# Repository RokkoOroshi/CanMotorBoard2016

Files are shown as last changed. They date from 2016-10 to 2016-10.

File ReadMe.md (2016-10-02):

# CAN Motor Driver Board

can通信機能対応2chモータドライバ基板

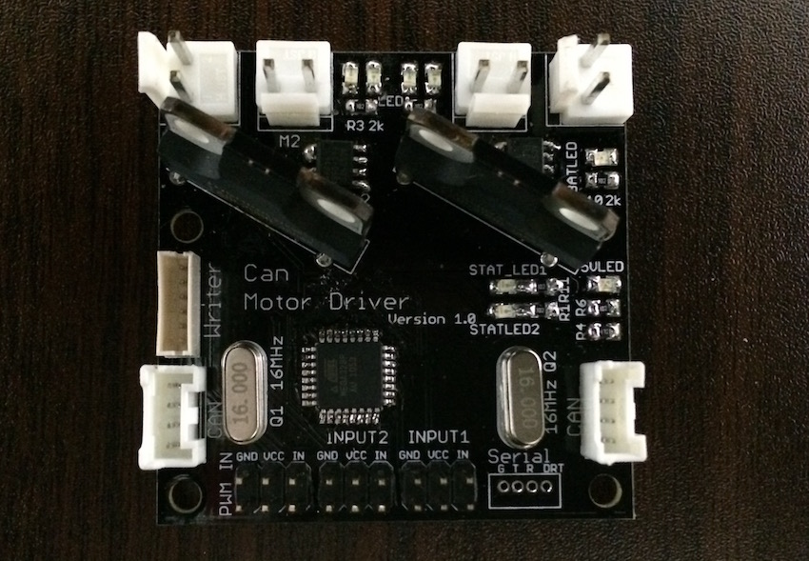
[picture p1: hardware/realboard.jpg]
基板


## IO

- DCモータ2ch制御 avg3.0A,peek4.5A (TA8429H使用)(放熱してないので無理です..)
- モータ電源ポート2個
- CAN通信ポート2個
- avr ISP 書き込みポート
- Arduino書き込み対応シリアル通信ポート
- 汎用入出力4ch(内2chはプルダウン済み)
- アナログ入力2ch
- 状態表示用LED 2ch

## 製作動機

- 製作負担軽減（と個人的な趣好）のために既存のユニバーサル基板からプリント基板への移行したい
- 配線の簡略化、基板との双方向通信実現のためにCAN通信を導入したい

## 製作時の配慮
- ストックが多数あるTA8429Hを使う
- PWM入力に対応し、今までと同じ方法でも使用できるようにする
- Arduino開発環境に対応し、初心者でも扱いやすいように

## License

- MIT

## 使用ライブラリ等

- CAN_BUS_Shield : MIT : https://github.com/Seeed-Studio/CAN_BUS_Shield
- MsTimer2 : LGPL : http://playground.arduino.cc/Main/MsTimer2
- pins_arduino.h : LGPL
- Arduino-SerialCommand : ? : https://github.com/kroimon/Arduino-SerialCommand

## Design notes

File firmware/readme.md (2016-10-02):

# CAN Motor Board Firmware

## Arduino IDE での使用方法
1. Arduino IDEをダウンロード・インストール
2. install.batを管理者として実行（Arduino IDEのフォルダ下に必要なファイルのシンボリックリンクを作ってる）
3. Arduino IDEのボード選択メニューで"RokkoOroshiCanMotorBoard"を選択

これで各ピンのシンボルが自動で定義され、各種ライブラリをincludeできるようになる。

また、この基板はArduinoProMini互換であるが、ブートローダーは書き込み速度を通常より高速にしたものを使用しているため、IDEでArduinoProMiniを選択した場合書き込みできないので注意。

## ライブラリ
Arduino IDEのメニュー include library から選択できるようになっているはず。

現状、依存ライブラリをhoge.ino内でincludeしないとコンパイルエラーになる

### Motor
* 基板に搭載された２つのモーター出力を制御する関数を定義している
* モーターの出力状態を管理するために、この関数を通じてモーターを制御すること。

### CanCommunication

* CAN上で各ノードが相互に通信するためのライブラリ
* 通信規格は独自の簡易的なものを使用、詳細はcan_communication_def.h参照
* SPI.h(標準ライブラリ), mcp_can.h(CAN_BUS_SHEILDライブラリ) に依存

## その他
* このフォルダ下にhardware_profile.h, can_communication_dfe.hがあるが、これは内容確認用に置いているだけ。RokkoOroshiCanMotorBoard下の深いところに同じファイルがあり、ArduinoIDEではそちらを参照している。このフォルダ下のものは最新でない可能性があるので注意。
* ピン配置はhardware_profile.hを見ると早い
* can_communication_defには通信規格を書いている

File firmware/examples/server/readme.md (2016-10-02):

# 4WD ロボット制御サンプル

* 基板二つを接続して4WDの足回りを動かせるようにする
* 前二つ、後ろ二つをそれぞれ同じ基板に接続
* 右モーターM1, 左モーターM2

#server

* pcで動く
* nodejs 使用

~~~
cd server
npm install
node main.js
# 表示されるリストからシリアル通信の接続先を選択
# ブラウザでlocalhost:8080 にアクセス
~~~

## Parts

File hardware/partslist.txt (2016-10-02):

抵抗

R1	1k	状態LED
R2	10k	MCP2515RESETプルアップ
R3	1k	モータ動作方向LED
R4	4.7k	CAN通信slope
R5	1k	モータ動作方向LED
R6	1k	ロジック電源LED
R7	1k	PWM入力プルダウン
R8	10k	マイコンRESETプルアップ
R9	1k	PWM入力プルダウン
R10	1k	モータ電源LED
R11	1k	状態LED
R14	2k	モータ電源電圧検出用分圧
R15	1k	モータ電源電圧検出用分圧

1k	9個
2k	1個
4.7k	1個
10k	2個

コンデンサ

C1	0.1uF	Arduino書き込み用DRT
C2	0.1uF	パスコン
C3	22pF	水晶発信器負荷
C4	22pF	 ..
C5	22pF	 ..
C6	22pF	 ..

0.1uF	2個
22pF	4個

その他
ATMega328p	1個	メインマイコン
TA8429H		2個	モータドライバ
MCP2551		1個	CAN通信
MCP2515		1個	CAN通信
ACS712		2個	電流センサ（オプション的扱い）
水晶発信器16MHz	2個
チップLED	8個	モータ方向x4, 電源x2, 汎用x2
ダイオード	1個	PWM入力ポートの電源逆流対策
B2P-VH		4個	モータ、モータ電源
B4B-ZR		1個	Arduino書き込み、シリアル通信
B6B-ZR		1個	ISP書き込み
B4B-PASK	2個	CAN通信
ピンヘッダ2x3	3個	PWMIN,ADC,DIO

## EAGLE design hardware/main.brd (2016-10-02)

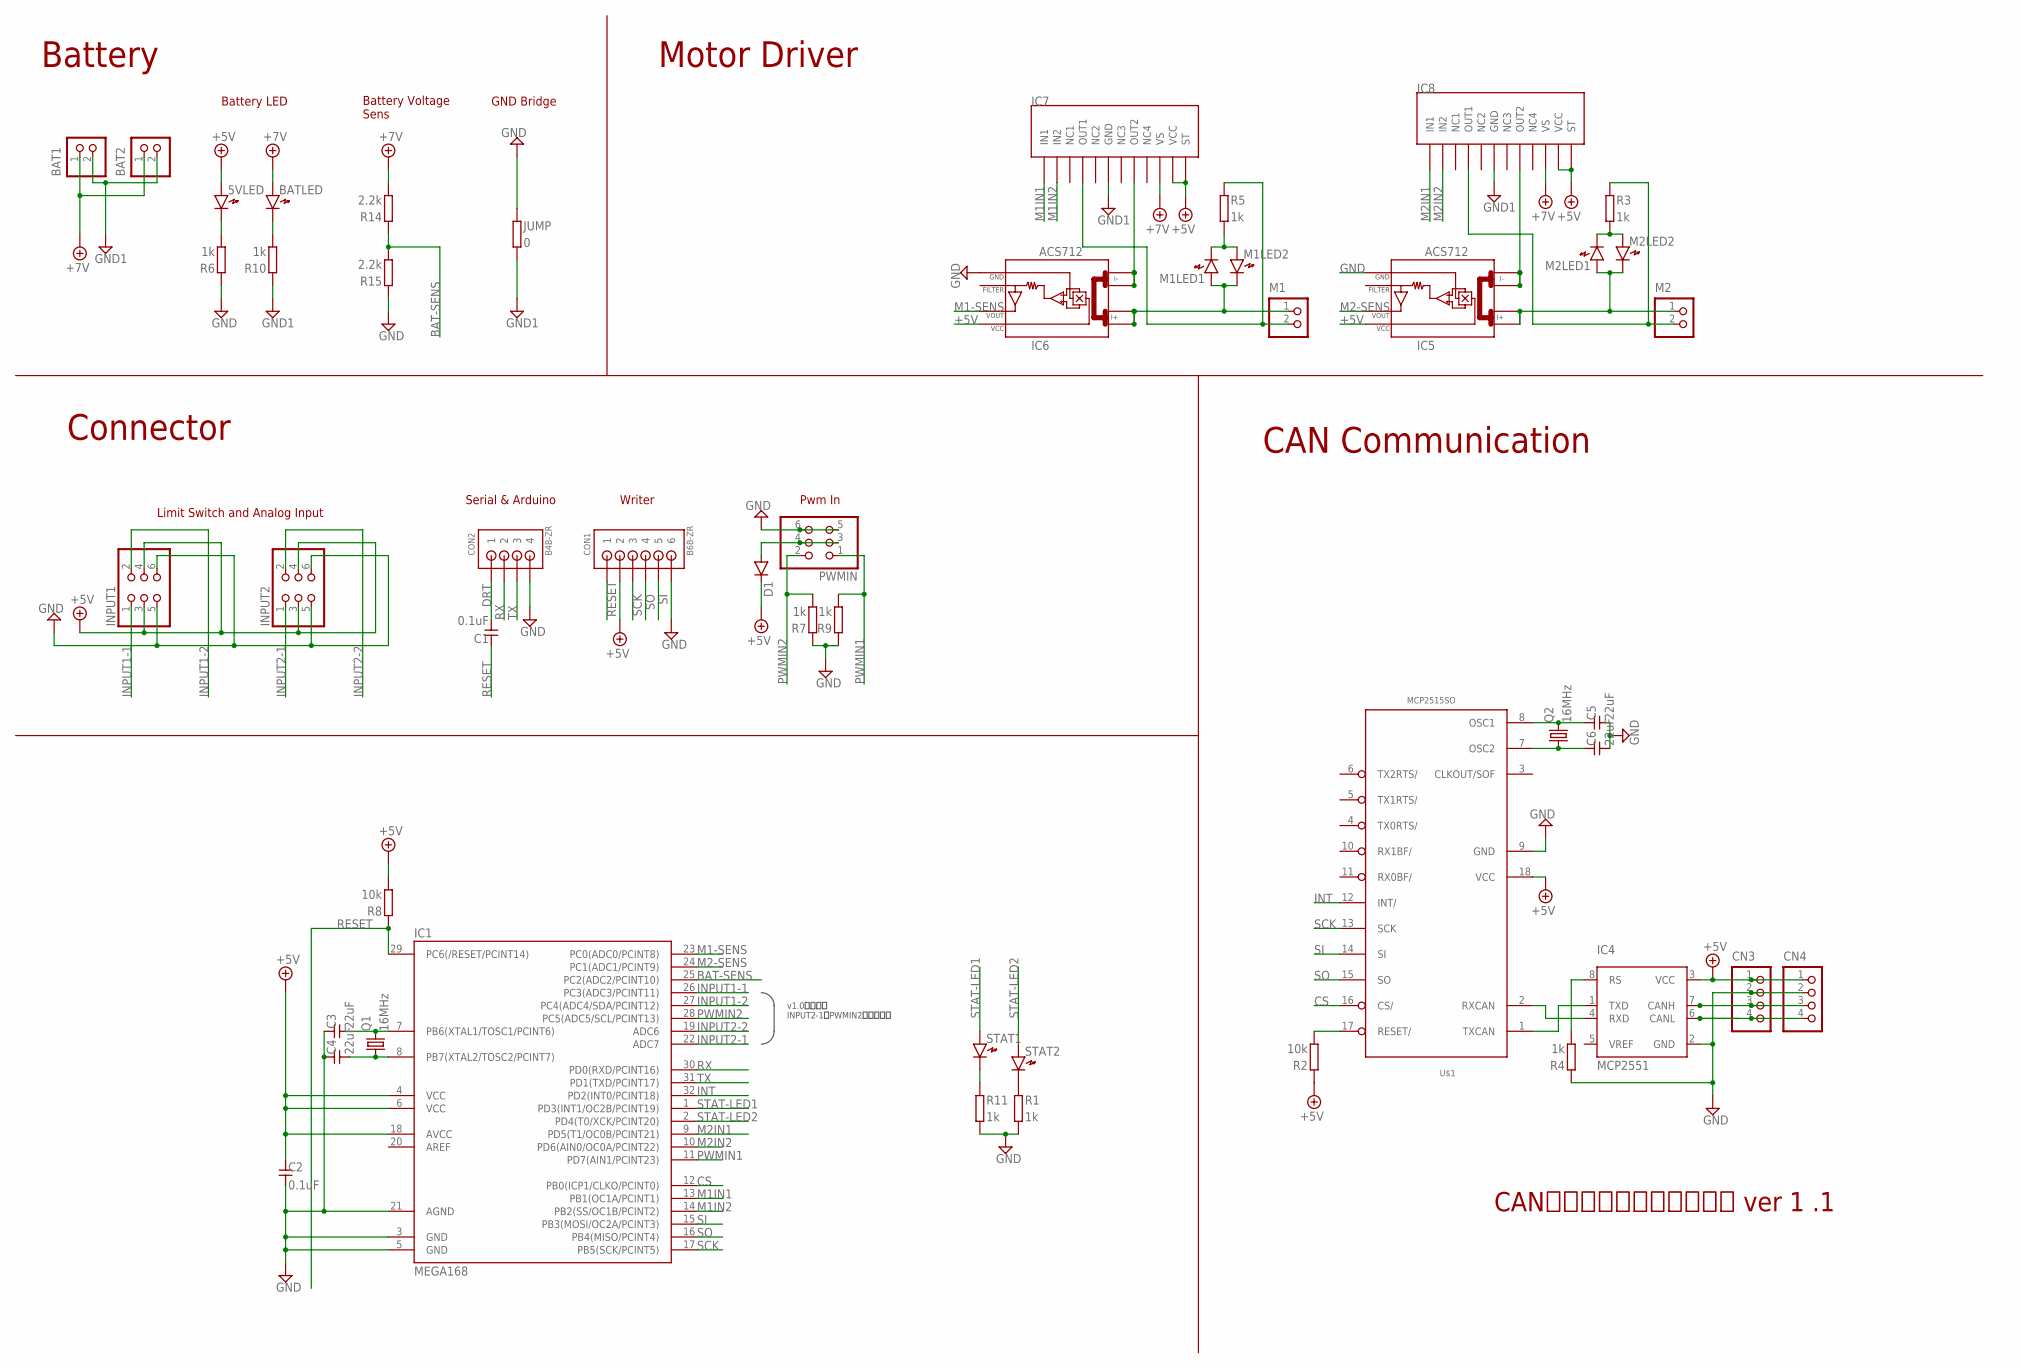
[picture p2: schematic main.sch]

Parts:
5VLED: LED2012
BAT1, BAT2: B2P-VH
BATLED: LED2012
C1, C2: 0.1uF; SMD2012
C3, C4, C5, C6: 22uF; SMD2012
CN3, CN4: B4B-PH-K-S
CON1: B6B-ZR
CON2: B4B-ZR
D1: DIODESOD123; SOD-123
IC1: MEGA168; TQFP32-08
IC4: MCP2551; SOIC
IC5, IC6: ACS712; SO08
IC7, IC8: TA8429H
INPUT1, INPUT2: PINHD-2X3; 2X03
JUMP: 0; SMD2012
M1, M2: B2P-VH
M1LED1, M1LED2, M2LED1, M2LED2: LED2012
PWMIN: PINHD-2X3; 2X03
Q1, Q2: 16MHz; HC49/S
R1, R3, R4, R5, R6, R7, R9, R10, R11: 1k; SMD2012
R2, R8: 10k; SMD2012
R14, R15: 2.2k; SMD2012
STAT1, STAT2: LED2012
U$1: MCP2515SO; SO18L

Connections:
+5V: 5VLED.A, C2.1, CN3.1, CN4.1, CON1.2, D1.C, IC1.4 (VCC), IC1.6 (VCC), IC1.18 (AVCC), IC4.3 (VCC), IC5.8 (VCC), IC6.8 (VCC), IC7.P$11 (VCC), IC7.P$12 (ST), IC8.P$11 (VCC), IC8.P$12 (ST), INPUT1.3, INPUT1.4, INPUT2.3, INPUT2.4, R2.1, R8.2, U$1.18 (VCC)
+7V: BAT1.1, BAT2.1, BATLED.A, IC7.P$10 (VS), IC8.P$10 (VS), R14.2
BAT-SENS: IC1.25 (PC2(ADC2/PCINT10)), R14.1, R15.2
CS: IC1.12 (PB0(ICP1/CLKO/PCINT0)), U$1.16 (CS/)
DRT: C1.2, CON2.1
GND: C2.2, C3.1, C4.1, C5.2, C6.2, CN3.2, CN4.2, CON1.6, CON2.4, IC1.3 (GND), IC1.5 (GND), IC1.21 (AGND), IC4.2 (GND), IC5.5 (GND), IC6.5 (GND), INPUT1.5, INPUT1.6, INPUT2.5, INPUT2.6, JUMP.1, PWMIN.5, PWMIN.6, R1.2, R4.1, R6.1, R7.1, R9.1, R11.2, R15.1, U$1.9 (GND)
INPUT1-1: IC1.26 (PC3(ADC3/PCINT11)), INPUT1.1
INPUT1-2: IC1.27 (PC4(ADC4/SDA/PCINT12)), INPUT1.2
INPUT2-1: IC1.22 (ADC7), INPUT2.1
INPUT2-2: IC1.19 (ADC6), INPUT2.2
INT: IC1.32 (PD2(INT0/PCINT18)), U$1.12 (INT/)
M1-SENS: IC1.23 (PC0(ADC0/PCINT8)), IC6.7 (VOUT)
M1IN1: IC1.13 (PB1(OC1A/PCINT1)), IC7.P$1 (IN1)
M1IN2: IC1.14 (PB2(SS/OC1B/PCINT2)), IC7.P$2 (IN2)
M2-SENS: IC1.24 (PC1(ADC1/PCINT9)), IC5.7 (VOUT)
M2IN1: IC1.9 (PD5(T1/OC0B/PCINT21)), IC8.P$1 (IN1)
M2IN2: IC1.10 (PD6(AIN0/OC0A/PCINT22)), IC8.P$2 (IN2)
MGND: BAT1.2, BAT2.2, IC7.P$6 (GND), IC8.P$6 (GND), JUMP.2, R10.1
unnamed: C3.2, IC1.7 (PB6(XTAL1/TOSC1/PCINT6)), Q1.2
unnamed: C4.2, IC1.8 (PB7(XTAL2/TOSC2/PCINT7)), Q1.1
unnamed: IC8.P$4 (OUT1), M2.2, R3.1
unnamed: IC6.1 (I+_0), IC6.2 (I+_1), M1.1, M1LED1.A, M1LED2.K
unnamed: D1.A, PWMIN.3, PWMIN.4
unnamed: IC5.1 (I+_0), IC5.2 (I+_1), M2.1, M2LED1.A, M2LED2.K
unnamed: IC4.1 (TXD), U$1.1 (TXCAN)
unnamed: IC4.4 (RXD), U$1.2 (RXCAN)
unnamed: 5VLED.K, R6.2
unnamed: R1.1, STAT2.K
unnamed: CN3.4, CN4.4, IC4.6 (CANL)
unnamed: CN3.3, CN4.3, IC4.7 (CANH)
unnamed: M1LED1.K, M1LED2.A, R5.2
unnamed: IC7.P$4 (OUT1), M1.2, R5.1
unnamed: R2.2, U$1.17 (RESET/)
unnamed: M2LED1.K, M2LED2.A, R3.2
unnamed: C6.1, Q2.1, U$1.7 (OSC2)
unnamed: BATLED.K, R10.2
unnamed: IC6.3 (I-_0), IC6.4 (I-_1), IC7.P$8 (OUT2)
unnamed: IC5.3 (I-_0), IC5.4 (I-_1), IC8.P$8 (OUT2)
unnamed: C5.1, Q2.2, U$1.8 (OSC1)
unnamed: IC4.8 (RS), R4.2
unnamed: R11.1, STAT1.K
PWMIN1: IC1.11 (PD7(AIN1/PCINT23)), PWMIN.1, R9.2
PWMIN2: IC1.28 (PC5(ADC5/SCL/PCINT13)), PWMIN.2, R7.2
RESET: C1.1, CON1.1, IC1.29 (PC6(/RESET/PCINT14)), R8.1
RX: CON2.2, IC1.30 (PD0(RXD/PCINT16))
SCK: CON1.3, IC1.17 (PB5(SCK/PCINT5)), U$1.13 (SCK)
SI: CON1.5, IC1.15 (PB3(MOSI/OC2A/PCINT3)), U$1.14 (SI)
SO: CON1.4, IC1.16 (PB4(MISO/PCINT4)), U$1.15 (SO)
STAT-LED1: IC1.1 (PD3(INT1/OC2B/PCINT19)), STAT1.A
STAT-LED2: IC1.2 (PD4(T0/XCK/PCINT20)), STAT2.A
TX: CON2.3, IC1.31 (PD1(TXD/PCINT17))

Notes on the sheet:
Limit Switch and Analog Input
Writer
CAN通信対応モータドライバ ver 1 .1
Battery
Motor Driver
CAN Communication
Connector
GND Bridge
Battery Voltage Sens
Battery LED
Serial & Arduino
Pwm In
v1.0から変更 INPUT2-1とPWMIN2を入れ替え

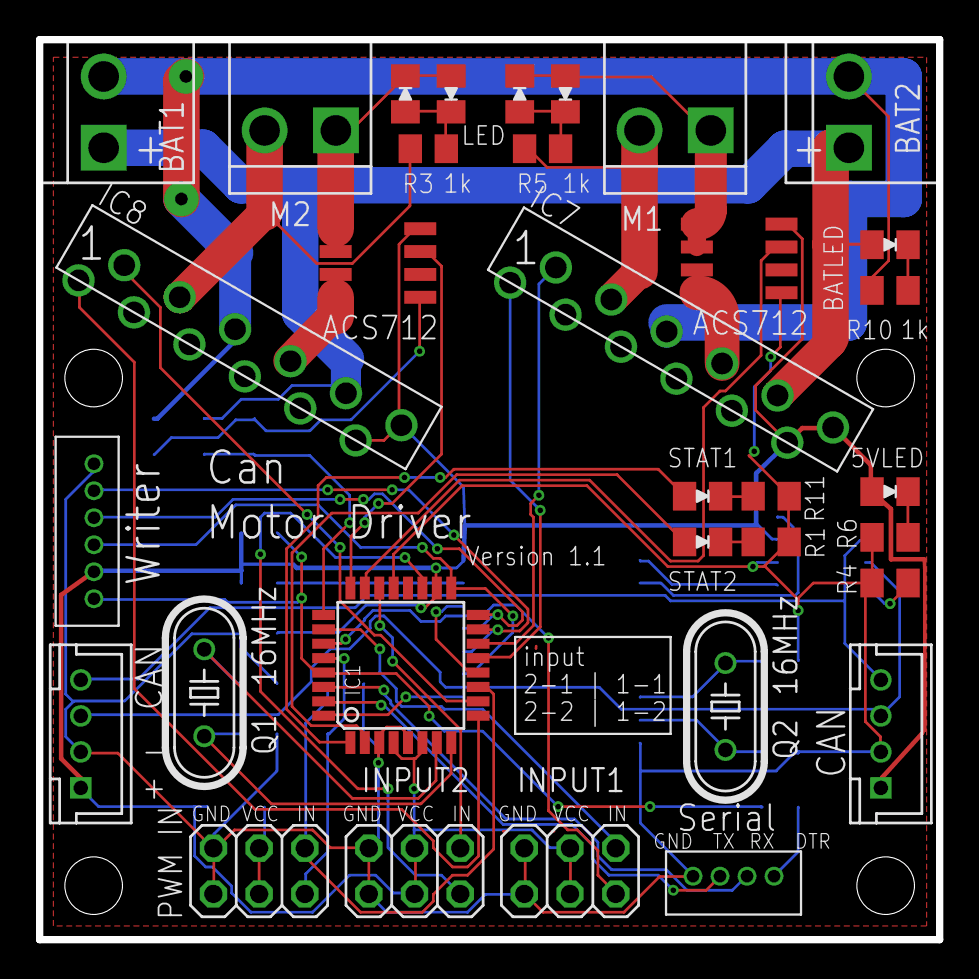
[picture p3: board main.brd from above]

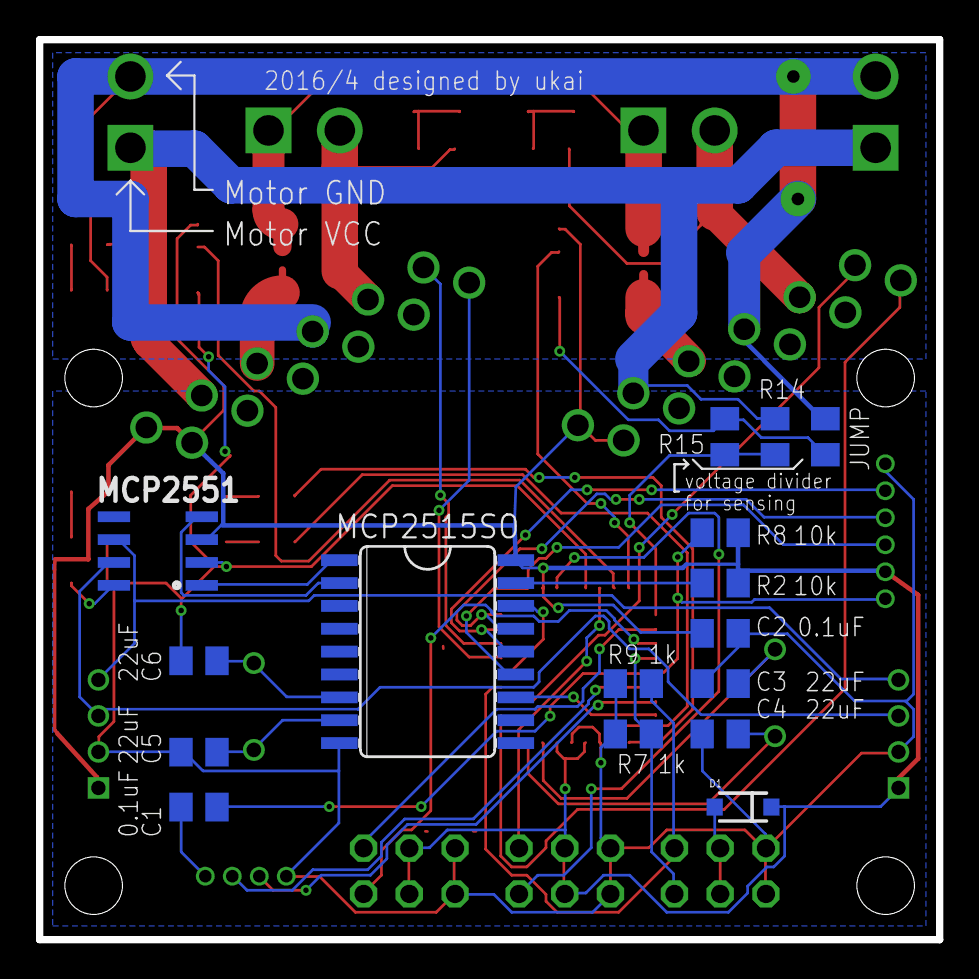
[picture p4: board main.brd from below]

Board: 2 copper layers, 50.0 x 50.0 mm, 49 parts (16 on the bottom side), 51 nets.

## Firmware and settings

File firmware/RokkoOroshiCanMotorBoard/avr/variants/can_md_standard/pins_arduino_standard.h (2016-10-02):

/*
  pins_arduino.h - Pin definition functions for Arduino
  Part of Arduino - http://www.arduino.cc/

  Copyright (c) 2007 David A. Mellis

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
  $Id: wiring.h 249 2007-02-03 16:52:51Z mellis $
*/

#ifndef Pins_Arduino_Standard_h
#define Pins_Arduino_Standard_h

#include <avr/pgmspace.h>

#define NUM_DIGITAL_PINS            20
#define NUM_ANALOG_INPUTS           6
#define analogInputToDigitalPin(p)  ((p < 6) ? (p) + 14 : -1)

#if defined(__AVR_ATmega8__)
#define digitalPinHasPWM(p)         ((p) == 9 || (p) == 10 || (p) == 11)
#else
#define digitalPinHasPWM(p)         ((p) == 3 || (p) == 5 || (p) == 6 || (p) == 9 || (p) == 10 || (p) == 11)
#endif

static const uint8_t SS   = 10;
static const uint8_t MOSI = 11;
static const uint8_t MISO = 12;
static const uint8_t SCK  = 13;

static const uint8_t SDA = 18;
static const uint8_t SCL = 19;
#define LED_BUILTIN 13

static const uint8_t A0 = 14;
static const uint8_t A1 = 15;
static const uint8_t A2 = 16;
static const uint8_t A3 = 17;
static const uint8_t A4 = 18;
static const uint8_t A5 = 19;
static const uint8_t A6 = 20;
static const uint8_t A7 = 21;

#define digitalPinToPCICR(p)    (((p) >= 0 && (p) <= 21) ? (&PCICR) : ((uint8_t *)0))
#define digitalPinToPCICRbit(p) (((p) <= 7) ? 2 : (((p) <= 13) ? 0 : 1))
#define digitalPinToPCMSK(p)    (((p) <= 7) ? (&PCMSK2) : (((p) <= 13) ? (&PCMSK0) : (((p) <= 21) ? (&PCMSK1) : ((uint8_t *)0))))
#define digitalPinToPCMSKbit(p) (((p) <= 7) ? (p) : (((p) <= 13) ? ((p) - 8) : ((p) - 14)))

#define digitalPinToInterrupt(p)  ((p) == 2 ? 0 : ((p) == 3 ? 1 : NOT_AN_INTERRUPT))

#ifdef ARDUINO_MAIN

// On the Arduino board, digital pins are also used
// for the analog output (software PWM).  Analog input
// pins are a separate set.

// ATMEL ATMEGA8 & 168 / ARDUINO
//
//                  +-\/-+
//            PC6  1|    |28  PC5 (AI 5)
//      (D 0) PD0  2|    |27  PC4 (AI 4)
//      (D 1) PD1  3|    |26  PC3 (AI 3)
//      (D 2) PD2  4|    |25  PC2 (AI 2)
// PWM+ (D 3) PD3  5|    |24  PC1 (AI 1)
//      (D 4) PD4  6|    |23  PC0 (AI 0)
//            VCC  7|    |22  GND
//            GND  8|    |21  AREF
//            PB6  9|    |20  AVCC
//            PB7 10|    |19  PB5 (D 13)
// PWM+ (D 5) PD5 11|    |18  PB4 (D 12)
// PWM+ (D 6) PD6 12|    |17  PB3 (D 11) PWM
//      (D 7) PD7 13|    |16  PB2 (D 10) PWM
//      (D 8) PB0 14|    |15  PB1 (D 9) PWM
//                  +----+
//
// (PWM+ indicates the additional PWM pins on the ATmega168.)

// ATMEL ATMEGA1280 / ARDUINO
//
// 0-7 PE0-PE7   works
// 8-13 PB0-PB5  works
// 14-21 PA0-PA7 works 
// 22-29 PH0-PH7 works
// 30-35 PG5-PG0 works
// 36-43 PC7-PC0 works
// 44-51 PJ7-PJ0 works
// 52-59 PL7-PL0 works
// 60-67 PD7-PD0 works
// A0-A7 PF0-PF7
// A8-A15 PK0-PK7


// these arrays map port names (e.g. port B) to the
// appropriate addresses for various functions (e.g. reading
// and writing)
const uint16_t PROGMEM port_to_mode_PGM[] = {
	NOT_A_PORT,
	NOT_A_PORT,
	(uint16_t) &DDRB,
	(uint16_t) &DDRC,
	(uint16_t) &DDRD,
};

const uint16_t PROGMEM port_to_output_PGM[] = {
	NOT_A_PORT,
	NOT_A_PORT,
	(uint16_t) &PORTB,
	(uint16_t) &PORTC,
	(uint16_t) &PORTD,
};

const uint16_t PROGMEM port_to_input_PGM[] = {
	NOT_A_PORT,
	NOT_A_PORT,
	(uint16_t) &PINB,
	(uint16_t) &PINC,
	(uint16_t) &PIND,
};

const uint8_t PROGMEM digital_pin_to_port_PGM[] = {
	PD, /* 0 */
	PD,
	PD,
	PD,
	PD,
	PD,
	PD,
	PD,
	PB, /* 8 */
	PB,
	PB,
	PB,
	PB,
	PB,
	PC, /* 14 */
	PC,
	PC,
	PC,
	PC,
	PC,
};

const uint8_t PROGMEM digital_pin_to_bit_mask_PGM[] = {
	_BV(0), /* 0, port D */
	_BV(1),
	_BV(2),
	_BV(3),
	_BV(4),
	_BV(5),
	_BV(6),
	_BV(7),
	_BV(0), /* 8, port B */
	_BV(1),
	_BV(2),
	_BV(3),
	_BV(4),
	_BV(5),
	_BV(0), /* 14, port C */
	_BV(1),
	_BV(2),
	_BV(3),
	_BV(4),
	_BV(5),
};

const uint8_t PROGMEM digital_pin_to_timer_PGM[] = {
	NOT_ON_TIMER, /* 0 - port D */
	NOT_ON_TIMER,
	NOT_ON_TIMER,
	// on the ATmega168, digital pin 3 has hardware pwm
#if defined(__AVR_ATmega8__)
	NOT_ON_TIMER,
#else
	TIMER2B,
#endif
	NOT_ON_TIMER,
	// on the ATmega168, digital pins 5 and 6 have hardware pwm
#if defined(__AVR_ATmega8__)
	NOT_ON_TIMER,
	NOT_ON_TIMER,
#else
	TIMER0B,
	TIMER0A,
#endif
	NOT_ON_TIMER,
	NOT_ON_TIMER, /* 8 - port B */
	TIMER1A,
	TIMER1B,
#if defined(__AVR_ATmega8__)
	TIMER2,
#else
	TIMER2A,
#endif
	NOT_ON_TIMER,
	NOT_ON_TIMER,
	NOT_ON_TIMER,
	NOT_ON_TIMER, /* 14 - port C */
	NOT_ON_TIMER,
	NOT_ON_TIMER,
	NOT_ON_TIMER,
	NOT_ON_TIMER,
};

#endif
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

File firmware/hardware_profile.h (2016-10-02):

#ifndef HARDWARE_PROFILE_H
#define HARDWARE_PROFILE_H

/*
  Arduino - AVR
  ---------
  D0  - PD0
  D1  - PD1
  D2  - PD2
  D3  - PD3
  D4  - PD4
  D5  - PD5
  D6  - PD6
  D7  - PD7
  ---------
  D8  - PB0
  D9  - PB1
  D10 - PB2
  D11 - PB3
  D12 - PB4
  D13 - PB5
  ---------
  A0  - PC0
  A1  - PC1
  A2  - PC2
  A3  - PC3
  A4  - PC4
  A5  - PC5
  (32pin Only)
  A6  - ADC6
  A7  - ADC7
 */


// Digital Pin
static const uint8_t SPI_CS   =  8;
static const uint8_t SPI_MOSI = 11;
static const uint8_t SPI_MISO = 12;
static const uint8_t SPI_SCK  = 13;

static const uint8_t CAN_INT  =  2;
static const uint8_t CAN_CS   =  8;
static const uint8_t CAN_MOSI = 11;
static const uint8_t CAN_MISO = 12;
static const uint8_t CAN_SCK  = 13;

static const uint8_t RX       =  0;
static const uint8_t TX       =  1;

static const uint8_t STAT_LED1=  3;
static const uint8_t STAT_LED2=  4;

static const uint8_t M1IN1    =  9;
static const uint8_t M1IN2    = 10;
static const uint8_t M2IN1    =  5;
static const uint8_t M2IN2    =  6;

static const uint8_t PWMIN1   =  7;
static const uint8_t PWMIN2   = 19;

// Analog
static const uint8_t M1_SENS  = 14; // A0
static const uint8_t M2_SENS  = 15; // A1
static const uint8_t BAT_SENS = 16; // A2

static const uint8_t INPUT1_1 = 17;
static const uint8_t INPUT1_2 = 18;

static const uint8_t INPUT2_1 = 21; // A7
static const uint8_t INPUT2_2 = 20; // A6

#endif

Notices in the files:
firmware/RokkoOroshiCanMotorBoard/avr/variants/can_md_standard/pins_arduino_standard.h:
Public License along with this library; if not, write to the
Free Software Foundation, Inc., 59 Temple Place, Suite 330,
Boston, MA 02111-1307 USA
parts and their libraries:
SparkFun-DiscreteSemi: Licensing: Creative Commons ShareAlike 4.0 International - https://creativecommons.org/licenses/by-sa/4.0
